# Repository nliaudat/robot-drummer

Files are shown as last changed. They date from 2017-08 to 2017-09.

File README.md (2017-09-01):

# robot-drummer
### An Arduino robotic drummer
*A funny hack for carnival 2015*

This is an automated, self playing drum machine, which can play an external midi source or preloaded patterns.
It uses door lock actuators cause it's strength, low cost and enduring

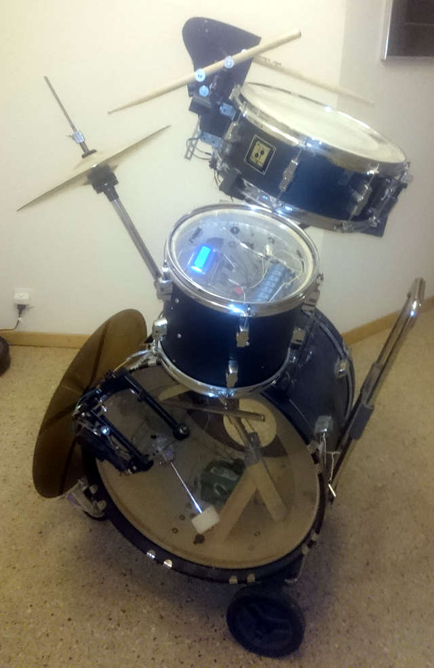
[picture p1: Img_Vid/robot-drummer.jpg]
Robot Drum


## Videos: 
* [Demo 1](https://www.youtube.com/watch?v=v6FhgfrhK6E)
* [Demo 2](https://www.youtube.com/watch?v=c7GqC0ccJ8k)
* [Remote controlled BPM increase](https://www.youtube.com/watch?v=mUgUUxgfKvs)
* [Remote controlled riff change](https://www.youtube.com/watch?v=ctWj6aDz2b4)
* [Hi-Hat cymbal moving](https://www.youtube.com/watch?v=tI9TEDjx_m8)

## Functionalities : 
* Infrared remote control to setup (speed, riff)
* 25 preloaded riffs, based on ascii drum tablatures
* Possible Midi source (not yet available cause Bluetooth module is not finished, midi source is working on lab)
* LCD display
* RGB ledstrip synced with music
* Each hit can be set as loud or normal

## Hardware BOM : 
### Drums
* Hi-hat (with pedal)
* Bass drum
* Snare drum

### Electronics : 
* 4x 12V Door Lock Actuator (2.8$ x 4)
* 1x 8-Channel Relay Module (3.3$)
* 1x Arduino Mega 2560 (7$)
* 1x LCD Display Module [1602] (2.15$)
* 1x Infrared Remote Controller Kit (0.7$)

### Optional : 
* 5V Voltage regulator (DIY manual included in Fritzing schema) (0.5$)
* RGB led strip (5$) (!! Do care : some are +12V and other -12V)

### Usage : 
Plug a 12V battery (cheap chinese lithium are available under 50$)

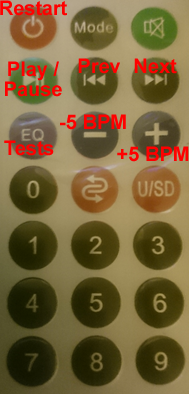
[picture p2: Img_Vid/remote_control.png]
IR remote control


## Construction : 
* "Img_Vid" folder for hardware
* "Arduino" folder for logics
* "Fritzing" folder for wiring and electronic bom
* [Relays and isolation considerations](8-channel_module.md)
* [Voltage regulator (optional but recommended)](voltage_regulator.md)

## Drum tab : 
* [How to make a new onboard riff based on drum tab](Drum-tab/drumtab.md)

## Got inspiration from : 
* [https://vitomakes.wordpress.com/2013/11/22/deep-inside-the-fork-o-drumbot/](https://vitomakes.wordpress.com/2013/11/22/deep-inside-the-fork-o-drumbot/)
* [http://blog.stef.be/drummerbot](http://blog.stef.be/drummerbot)
* [http://www.instructables.com/id/Arduino-Controlled-Robotic-Drum/?ALLSTEPS](http://www.instructables.com/id/Arduino-Controlled-Robotic-Drum/?ALLSTEPS)
* [http://www.instructables.com/id/Make-a-Beat-using-Solenoids/?ALLSTEPS](http://www.instructables.com/id/Make-a-Beat-using-Solenoids/?ALLSTEPS)
* [http://makezine.com/projects/make-robotic-drum-using-arduino-uno/](http://makezine.com/projects/make-robotic-drum-using-arduino-uno/)
* [http://nrqm.ca/robot-drummer/](http://nrqm.ca/robot-drummer/)

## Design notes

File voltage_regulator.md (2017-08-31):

## 12V Voltage regulator and fuse : 

### Concept
[+12 volts in]-->[1 ohm, 5 watt resistor]-->[1N5402 diode]-->[1000uF, 25v cap] --> [LM7805 ] --> [clean 5V]

### Sample
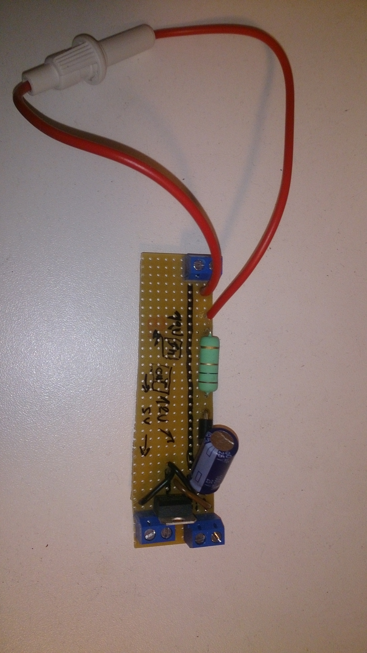
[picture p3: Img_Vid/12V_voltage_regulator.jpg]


### Schematic
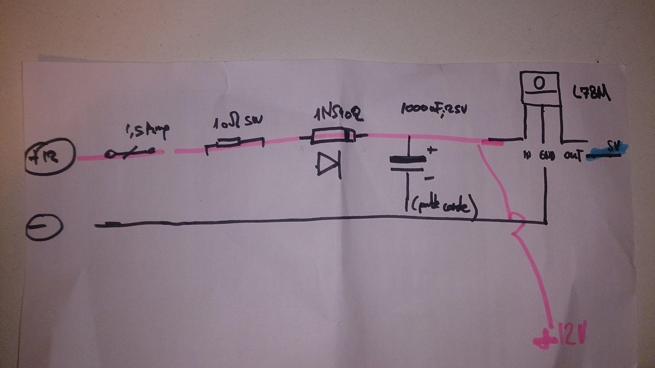
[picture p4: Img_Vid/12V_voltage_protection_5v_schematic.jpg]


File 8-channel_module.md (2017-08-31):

## 8 channels module

### Warning

Notice that relay board has a jumper between "Vcc" and "JD-Vcc". Remove it. For complete optical isolation, connect "Vcc" to Arduino +5 volts but do NOT connect Arduino Ground. Connect your Arduino Digital Output pins to "IN0", "IN1" etc. Connect a separate +5 supply to "JD-Vcc" and board Gnd

### References

* https://arduino-info.wikispaces.com/RelayIsolation
* https://www.forward.com.au/pfod/HomeAutomation/OnOffAddRelay/index.html

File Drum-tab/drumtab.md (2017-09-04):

## How to make a new onboard riff based on drum tab : 

### What are drum tabs ?

* https://en.wikipedia.org/wiki/Drum_tablature
* [Explanations] (http://www.cygnusproductions.com/rtp/drums/dtab_explanation.txt)

### Where to find samples ? 

* ./samples folder
* http://www.drumtabs.org/
* http://www.911tabs.com
* http://drumbum.com/drumtabs/

### How to code for the drummer: 

#### Sample code
```
const static char PROGMEM pattern_num[6][36] = { //36 = pattern lenght + 1 null terminator
  "|x-x-o-x-x-o-x-x-|o-x-x-o-x-x-o-x-|", //HH : hit-hat
  "|----o-----o-----|o-----o-----o---|", //SN : snare
  "|o-----o-o-----o-|o-----o-o-----o-|", //BS : bass
// |1eta2eta3eta4eta|1eta2eta3eta4eta| //
  "4:4 Bossa nova ", //name displayed on LCD
  "4" //tempo
};
```

#### Drumcodes 
```
"-" = nothing
"|" = end of measure
"x" = hit (snare or closed hi-hat)
"o" = hit on open hi-hat
"h" = hit on 1/2 open hi-hat
"p" = hi-hat pedal
"f" = hit with 2 hands (considered as simple hit)
```

**MAJ letter are for loud, min are for normal**

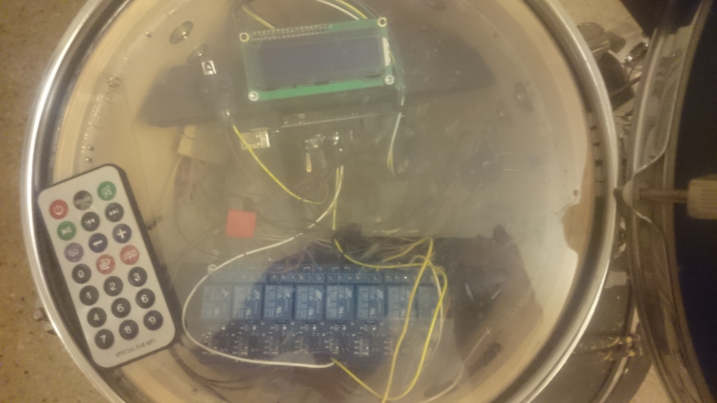
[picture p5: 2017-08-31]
Img_Vid/electronics.jpg

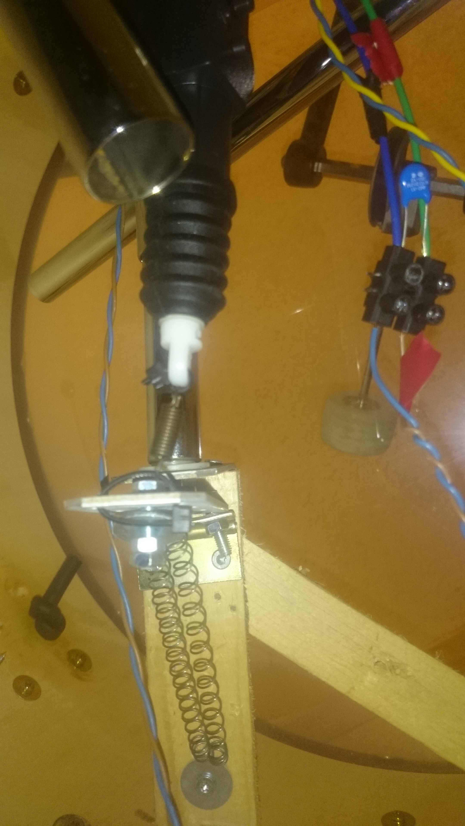
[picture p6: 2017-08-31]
Img_Vid/hi-hat_foot_pedal_actuator.jpg

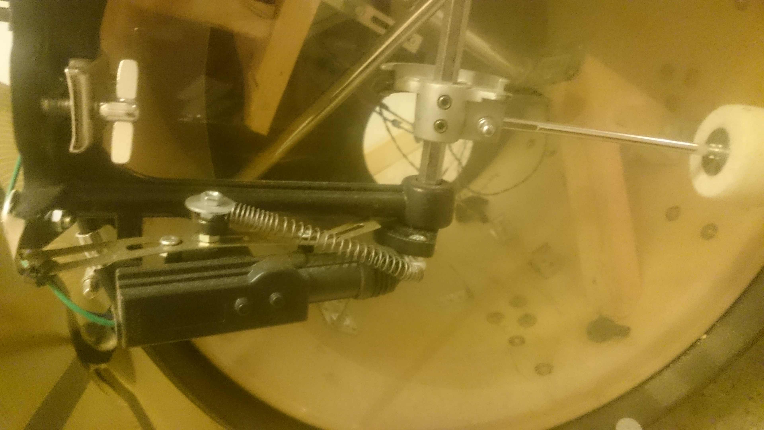
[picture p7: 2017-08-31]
Img_Vid/bass_actuator.jpg

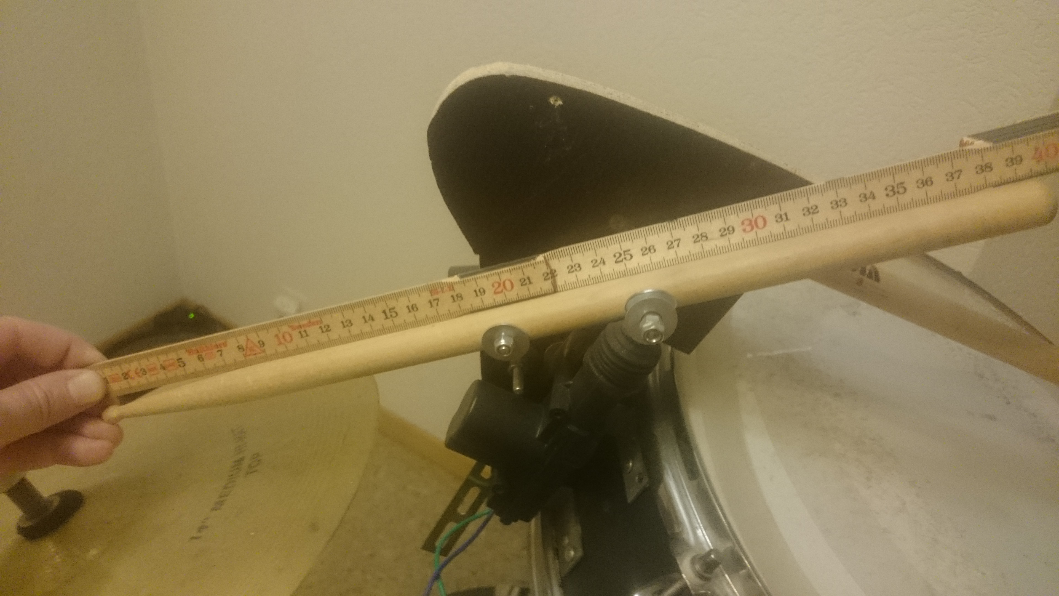
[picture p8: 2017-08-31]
Img_Vid/hi-hat_axle.jpg

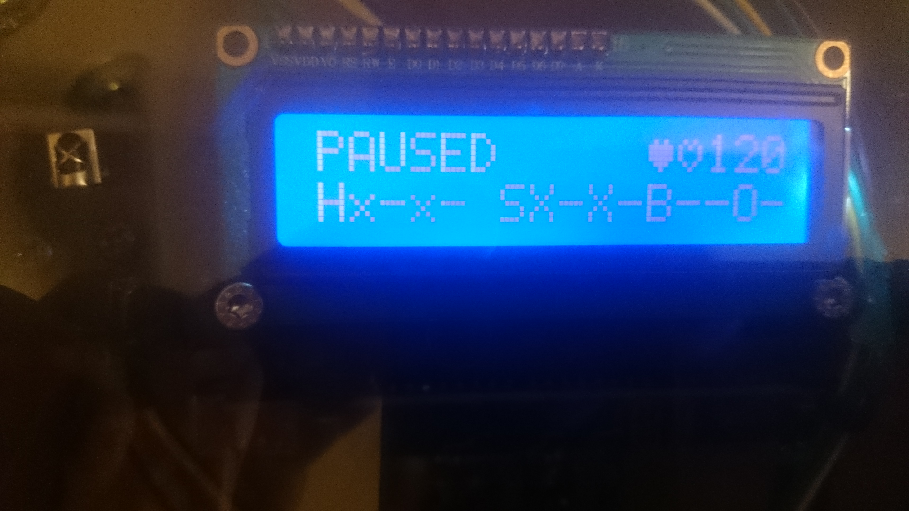
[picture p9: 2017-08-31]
Img_Vid/lcd.jpg

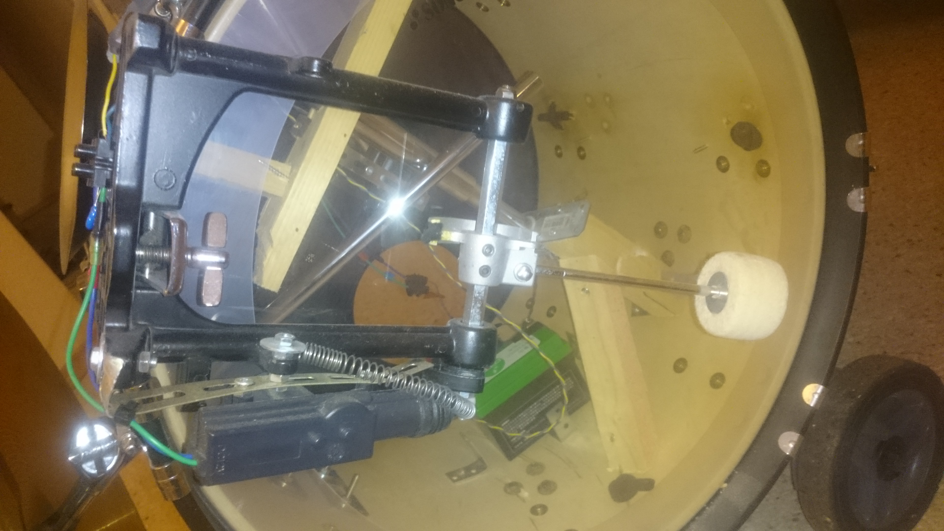
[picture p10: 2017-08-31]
Img_Vid/bass.jpg

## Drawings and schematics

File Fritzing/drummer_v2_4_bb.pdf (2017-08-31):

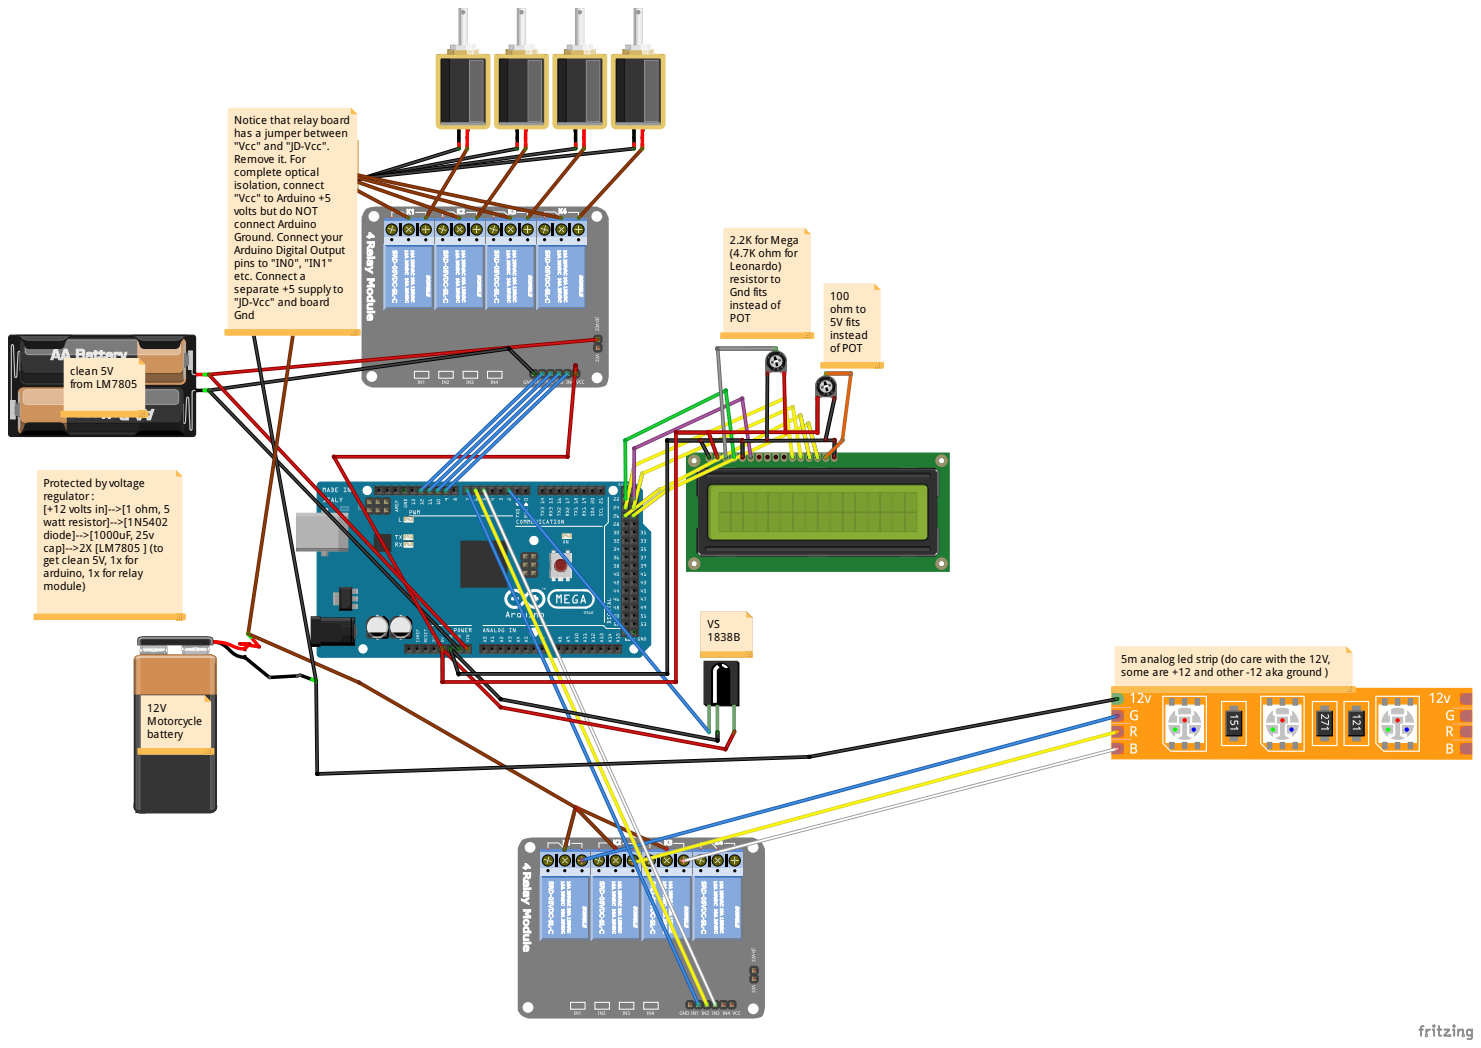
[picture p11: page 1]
tic; ela; uin; Digit; pin; ply; fit s instea; sis; fit s instead; cle; ycle; alo; rip; wit; volt a; ula; r: [+12 volts in ]; dio; ule

". Remove it. For complete optical isolation, connect "Vcc" to Arduino +5 volts but do NOT connect Arduino Ground. Connect yo

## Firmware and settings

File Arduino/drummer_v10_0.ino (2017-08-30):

/*
// *****************************************************************************
//                              robotic drummer
// *****************************************************************************
// 
// Nicolas Liaudat - 2015 - nliaudat[at]gmail(pt)com
//
// Got inspiration from : 
// https://vitomakes.wordpress.com/2013/11/22/deep-inside-the-fork-o-drumbot/
// http://blog.stef.be/drummerbot
// http://www.instructables.com/id/Arduino-Controlled-Robotic-Drum/?ALLSTEPS
// http://www.instructables.com/id/Make-a-Beat-using-Solenoids/?ALLSTEPS
// http://makezine.com/projects/make-robotic-drum-using-arduino-uno/
// http://nrqm.ca/robot-drummer/
//
*/

// can use midi serial source OR/AND preloaded patterns
//#define USE_SOURCE_MIDI
#define USE_SOURCE_PATTERN

      

      //When using the Arduino board with midi in, it’s necessary to set the baudrate to the midi standard of 31250. 
      //Unfortunately, this is a non-default baudrate so the Arduino Serial Monitor cannot display this serial data

#ifdef USE_SOURCE_MIDI //cannot debug with midi enabled
  static const bool MAIN_DEBUG = false;
#else
  static const bool MAIN_DEBUG = true; //if needed
#endif

#ifdef USE_SOURCE_PATTERN
  volatile bool PAUSE_PATTERN = false; //midi running
  //const int PATTERN[6]={1,2,3,4,5,99}; //used in switch_pattern(int num){
  volatile int CURRENT_PATTERN;
  const int MAX_PATTERN_NUM = 25; //not include template num 0
  volatile int BPM = 120;
  volatile bool BPM_blink= false;
#endif

///////////////////////////////////////////////////////////////////// Setup /////////////////////
void setup() {

   if(MAIN_DEBUG){

//#ifdef USE_SOURCE_MIDI
//        
//        Serial.println("MIDI Input : enabled");
//#else
//        Serial.println("MIDI Input : disabled");
//#endif

#ifdef USE_SOURCE_PATTERN
    #ifndef USE_SOURCE_MIDI
            Serial.begin(38400); // 31250 for midi, 38400 for serial debug
              while (!Serial) {
                ; // wait for serial port to connect. Needed for native USB port only
              }
    #endif
        Serial.println("main debug :");
        Serial.println("onboard PATTERNS : enabled");
#else
        Serial.println("onboard PATTERNS : disabled");
#endif
      
   }
  //Serial.begin(9600); 

#ifdef USE_SOURCE_PATTERN
    setup_drum_pattern();
#endif

  //setup_solenoid(); // pattern and midi read if defined
  setup_RELAYS();
  setup_lcd();
  setup_IR();
  //setup_ledstrip();
}

///////////////////////////////////////////////////////////////////// Loop /////////////////////
void loop() {

#ifdef USE_SOURCE_PATTERN
       if(PAUSE_PATTERN == true){
          loop_pattern();
          //loop_potentiometer_bpm();
       }//else{
        //loop_potentiometer_pattern();
       //}
#endif

     //loop_solenoid();
     loop_RELAYS();
     loop_IR();
     
     //loop_analog_buttons();

     
  

}

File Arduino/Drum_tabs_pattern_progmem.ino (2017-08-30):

/*
  // http://www.drumtabs.org/
  // ### Editors
  // http://domoritz.de/drummy/
  // http://whatang.org/
  //
  //
  // ### Samples
  // http://www.911tabs.com
  // http://drumbum.com/drumtabs/
  // http://www.911tabs.com/link/?6671161
*/

/*

  //http://www.cygnusproductions.com/rtp/drums/dtab_explanation.txt

  ## simple
  B = Bass-Drum
  S = Snare-Drum
  H = Hi-Hat
  C = Cymbal
  T = Tom

  ##
  HH|=Hi-Hat SN|=Snare
  BS|=Bass   FT|=Floor Tom
  T1|=Tom 1  C1|=Crash 1

  Cymbal              Hi-Hat           Snare
  C = crash           X = closed       X = hit
  R = ride            O = open         R = rimshot
  B = bell of ride    H = half-open    F = flam
  S = splash          P = with pedal   S = side stick
  T = china (trash)



*/



#ifdef USE_SOURCE_PATTERN



unsigned long INTERVAL = 0;

#ifdef USE_SOURCE_MIDI //cannot debug with midi enabled
static const bool PATTERN_DEBUG = false;
#else
static const bool PATTERN_DEBUG = false; //if needed
#endif



unsigned long previousMillis = 0;
unsigned long currentMillis ;

/// Store data in flash (program) memory instead of SRAM
// https://www.arduino.cc/en/Reference/PROGMEM

#include <avr/pgmspace.h>

//char * drumcode[7] = {"-", //nothing
//                      "|", //end of measure
//                      "x", //hit (snare or closed hi-hat)
//                      "o", //hit on open hi-hat
//                      "h", //hit on 1/2 open hi-hat
//                      "p", //hi-hat pedal
//                      "f"};// hit with 2 hands (considered as simple hit
//
//
//                       MAJ letter are for loud, min are for normal


static const int LOUD = 127;
static const int QUIET = 70;


//const static char PROGMEM pattern_null[6][19] ={ //6 params, 16 tempo char + 2 delimiter + 1 null terminator = 19
//   "|----------------|", //HH : hit-hat
//   "|----------------|", //SN : snare
//   "|----------------|", //BS : bass
// // |1eta2eta3eta4eta|
//   "Empty", //name max 10 chars
//   "4"//tempo : 4:4
//};

const static char PROGMEM pattern_0[6][53] = { //test pattern
  "|x---x---X---X---|o---o---O---O---|p---p---P---P---|", //HH
  "|o---o---O---O---|o-o-o-O-O-OoOoOo|o---o---O---O---|", //SN
  "|o---o---O---O---|o-o-o-O-O-OoOoOo|o---o---O---O---|", //BS
// |1eta2eta3eta4eta|1eta2eta3eta4eta|1eta2eta3eta4eta|
  "Test      ", //name max 10 chars
  "4" //tempo
};

const static char PROGMEM pattern_1[6][19] = {
  "|x-x-x-x-x-x-x-x-|", //HH
  "|----o-------o---|", //SN
  "|o-------o-o-----|", //BS
// |1eta2eta3eta4eta|
  "4:4 [1] 1m", //name
//"1234567890"
  "4" //tempo
};

const static char PROGMEM pattern_2[6][36] = {
  "|--x-x-x-x-x-x-x-|x-x-x-x-x-x-x-x-|", //HH
  "|----o-------o---|----o-o-----o---|", //SN
  "|o-------o-o---o-|--o-----o-o-----|", //BS
// |1eta2eta3eta4eta|1eta2eta3eta4eta|
  "4:4 [2] 2m", //name
//"1234567890"
  "4" //tempo
};


const static char PROGMEM pattern_3[6][36] = { //4:4
  "|x-x-x-x-x-x-x-x-|x-x-x-x-x-x-x-o-|", //HH
  "|----o-------o---|----o-------o---|", //SN
  "|o-o-----o-o---o-|o-o-----o-o-----|", //BS
// |1eta2eta3eta4eta|1eta2eta3eta4eta|
  "4:4 [3] 2m", //name
//"1234567890"
  "4" //tempo
};

const static char PROGMEM pattern_4[6][70] = { //4:4
  "|--x-x-x-x-x-x-x-|x-x-x-x-x-x-x-o-|--x-x-x-x-x-x-x-|x-x-x-x-x-x-x-o-|", //HH
  "|----o-------o---|----o-------o---|----o--o----o---|----o---o---o---|", //SN
  "|o-----o-o-----o-|o-----o-o-o-----|o-o-----o-o-----|o-o---o---o---o-|", //BS
// |1eta2eta3eta4eta|1eta2eta3eta4eta|1eta2eta3eta4eta|1eta2eta3eta4eta|
  "4:4 [4] 4m", //name
//"1234567890"
  "4" //tempo
};



const static char PROGMEM pattern_5[6][70] = { //4:4
  "|--x-x-x-x-x-x-x-|x-x-x-x-x-x-x-x-|x-x-x-x-x-x-x-x-|x-x-x-x-x-x-o--P|", //HH
  "|----o-------o---|----o-------o---|----o-------o---|----o-------o---|", //SN
  "|o-o---o---o---o-|--o-----o-o-----|o-o---o---o---o-|--o-----o-o-----|", //BS
// |1eta2eta3eta4eta|1eta2eta3eta4eta|1eta2eta3eta4eta|1eta2eta3eta4eta|
  "4:4 [5] 4m", //name
//"1234567890"
  "4" //tempo
};


const static char PROGMEM pattern_6[6][36] = { //4:4
  "|----X---X---X---|X---X---X---X---|", //HH
  "|----o-------o---|----o-------o---|", //SN
  "|o-o---o-o-o---o-|o-o---o-o-o-----|", //BS
// |1eta2eta3eta4eta|1eta2eta3eta4eta|
  "4:4 [6] 2m", //name
//"1234567890"
  "4" //tempo
};


const static char PROGMEM pattern_7[6][19] = { //4:4
  "|X---o---X---o---|", //HH
  "|----o--o-o--o---|", //SN
  "|o--o----o-oo--o-|", //BS
// |1eta2eta3eta4eta|
  "4:4 [7] 1m", //name
//"1234567890"
  "4" //tempo
};

const static char PROGMEM pattern_8[6][19] = { //4:4
  "|X---X---X---X---|", //HH
  "|----o---o---o---|", //SN
  "|o--o---o-o-o--o-|", //BS
// |1eta2eta3eta4eta|
  "4:4 [8] 1m", //name
//"1234567890"
  "4" //tempo
};


const static char PROGMEM pattern_9[6][70] = { //4:4
  "|--X-X-X-X-X-X-X-|X-X-X-X-X-X-X-X-|X-X-X-X-XXX-X-XX|XXXXX-X-XXX-X---|", //HH
  "|------O-----O---|------O-----O--O|------O-----O---|------O-----O-OO|", //SN
  "|O----O-----O----|O----O-----O----|O----O-----O----|O----O-----O-O--|", //BS
// |1eta2eta3eta4eta|1eta2eta3eta4eta|1eta2eta3eta4eta|1eta2eta3eta4eta|
  "4:4 [9] 4m", //name
//"1234567890"
  "4" //tempo
};


//Rage Against the Machine : Fistful of Steel
const static char PROGMEM pattern_10[6][70] = { //4:4
  "|x-O---x-x-O-x-O-|x-O-x-x-x-O-x-O-|x-O-x-x-x-O-x-O-|x-x-x-x-x-O-x-O-|", //HH
  "|----o----o--o---|----o----o--o---|----o----o--o---|----o--o----o---|", //SN
  "|o---------o---o-|oo--------o---o-|o---------o---o-|oo-o------o---o-|", //BS
// |1eta2eta3eta4eta|1eta2eta3eta4eta|1eta2eta3eta4eta|1eta2eta3eta4eta|
  "4:4 [10]4m", //name
//"1234567890"
  "4" //tempo
};


//Rage Against the Machine : Fistful of Steel
const static char PROGMEM pattern_11[6][70] = { //4:4
  "|x-x-x-x-x-x-x-x-|x-x-x-x-x-x-x-x-|x-x-x-x-x-x-x-x-|x-x-x-x-x-x-x-x-|", //HH
  "|----o-------o---|--o-o-------o---|----o-------o---|--o-o----o--o---|", //SN
  "|o-o---oo--o-----|o-----oo--o-----|o-o---oo--o-----|o-----oo--oo--o-|", //BS
// |1eta2eta3eta4eta|1eta2eta3eta4eta|1eta2eta3eta4eta|1eta2eta3eta4eta|
  "4:4 [11]4m", //name
//"1234567890"
  "4" //tempo
};

//Rage Against the Machine : Fistful of Steel
const static char PROGMEM pattern_12[6][70] = { //4:4
  "|--x-x-x-x-x-x-x-|--x-x-x-x-x-x-x-|--x-x-x-x-x-x-x-|--x-x-x-x-x-x-x-|", //HH
  "|----o-------o---|----o---oo--oo--|----o-------o---|----o---oo--oo--|", //SN
  "|--o--o--o--o---o|--o--o-o---o---o|--o--o--o--o---o|--o--o-o---o---o|", //BS
// |1eta2eta3eta4eta|1eta2eta3eta4eta|1eta2eta3eta4eta|1eta2eta3eta4eta|
  "4:4 [12]4m", //name
//"1234567890"
  "4" //tempo
};


// Rage Against the Machine : Township Rebellion
const static char PROGMEM pattern_13[6][19] = { //4:4
  "|--o-------o---o-|", //HH
  "|----s-------s---|", //SN
  "|o--o--o---o--o--|", //BS
// |1eta2eta3eta4eta|
  "4:4 [13]1m", //name
//"1234567890"
  "4" //tempo
};
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
